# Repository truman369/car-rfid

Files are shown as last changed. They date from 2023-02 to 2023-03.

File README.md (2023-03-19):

# RFID Car Lock

This project is an Arduino-based device that controls a car lock using an RFID reader. It allows for keyless entry to the car by reading an RFID tag and unlocking the doors if the tag matches the authorized tag in the system.

## Hardware Requirements

To build this project, I used the following components:

- Arduino Nano
- Ironlogic CP-Z-2 RFID 125 Khz reader
- Standard 5-wire car lock actuator
- TZT 5V 4 channel relay module
- Mini360 DC-DC step down converter
- Standard passive buzzer
- Breadboard, wires, male and female pins, jumper, button, screw connectors

## Circuit Diagram

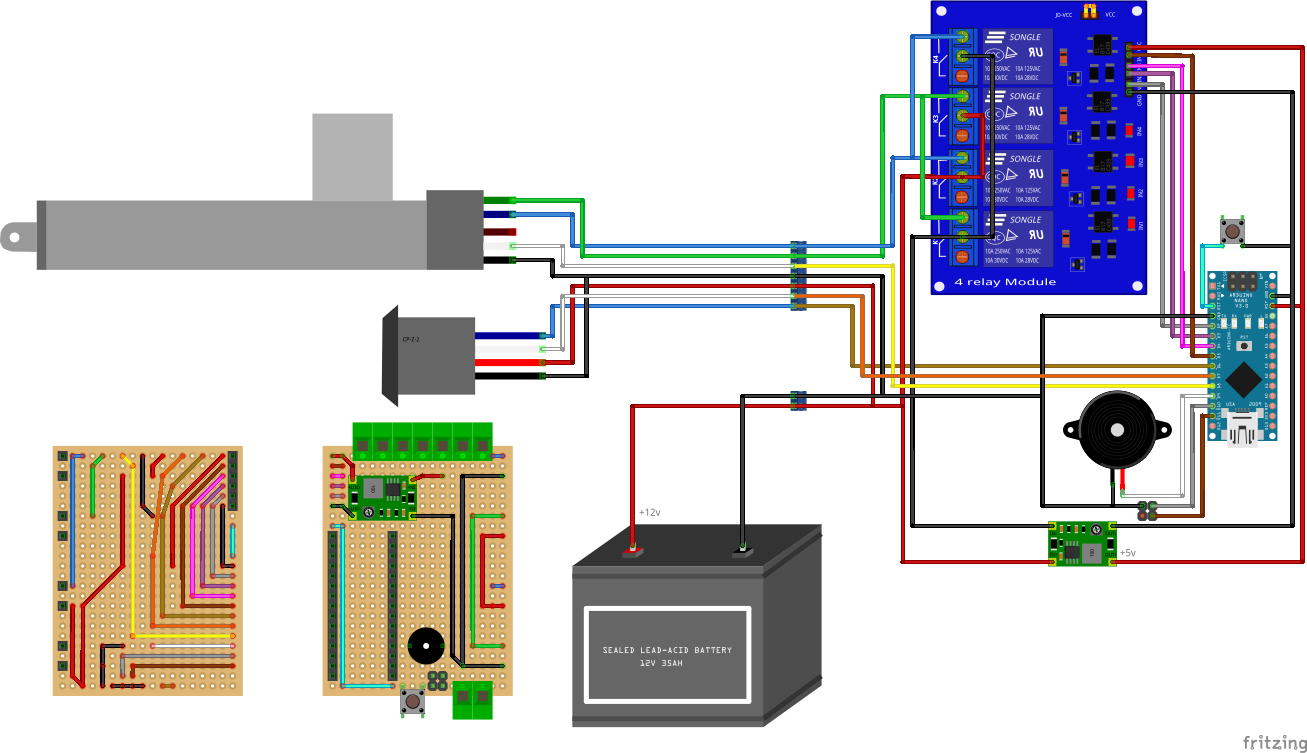
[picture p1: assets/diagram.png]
Circuit Diagram


Ironlogic CP-Z-2 reader operates in DS-1990A emulation mode and sends the key code via D1 (white) using the 1-wire protocol. D0 (blue) is used to wake up the Arduino controller from deep sleep mode.

The lock is controlled through a relay module by applying direct and inverted voltage to the actuator wires (green and blue). The white wire of the actuator is used to read the current lock position (open/closed).

The jumper is used to set the operating modes. The button is used to reboot the device. The buzzer is used for device status indication.

## Software Requirements

External libraries used in the project:
- [OneWire](https://github.com/paulstoffregen/OneWire)
- [LowPower](https://github.com/LowPowerLab/LowPower)

To build and upload the project, you can use the following components:

- [PlatformIO Core](https://docs.platformio.org/en/latest/core/installation.html)
- [Visual Studio Code](https://code.visualstudio.com/) 

## Installation

1. Clone the repository to your local machine.
2. Connect the Arduino to your computer using a USB cable.
3. Make sure that the Arduino is properly recognized by your system.
4. Open the project folder in Visual Studio Code.
5. In VS Code, open the Terminal and run the command `pio run` to build the project.

## Usage

Set up operating mode using the jumper and reboot the device.

Jumper Position

### Normal mode

No jumper or pins 3-4 are shorted. On startup the buzzer emits one short beep.

When applying an rfid key, if the key is authorized, the lock changes its state and the buzzer emits long high tone beep.

If the key is not authorized, or opening/closing the lock failed, the buzzer emits long low tone beep.

### Add keys

Jumper is set to short 2-4 pins. On startup the buzzer emits two short beeps: one medium and one high tone.

When applying an rfid key, one short beep sounds and device try to save the key. After that:

- Long high tone beep - the key was successfully written to memory.

- Long low tone beep - the key already exists, or max count of keys reached.

### Remove keys

Jumper is set to short 1-3 pins. On startup the buzzer emits three short beeps: one medium and two high tone.

When applying an rfid key, two short beep sounds and device try to remove the key from memory. After that:

- Long high tone beep - the key was successfully removed from memory.

- Long low tone beep - the key not found.

### Full reset

Jumper is set to short 1-2 pins. On startup the buzzer emits five short beeps: one medium tone and four high ones. After that, the device EEPROM is completely erased.

## 3D Printed Case

I made a very simple case for 3D printing, but it needs some modification in place. Here are STL files:

- [Lower Body](assets/car_rfid_case_1.stl)
- [Top Case](assets/car_rfid_case_2.stl)

## Additional images

- [Breadboard top](assets/breadboard_01.jpg)
- [Breadboard bottom](assets/breadboard_02.jpg)
- [Breadboard assembled](assets/breadboard_03.jpg)
- [3D-printed case](assets/case_01.jpg)
- [Case modification](assets/case_02.jpg)

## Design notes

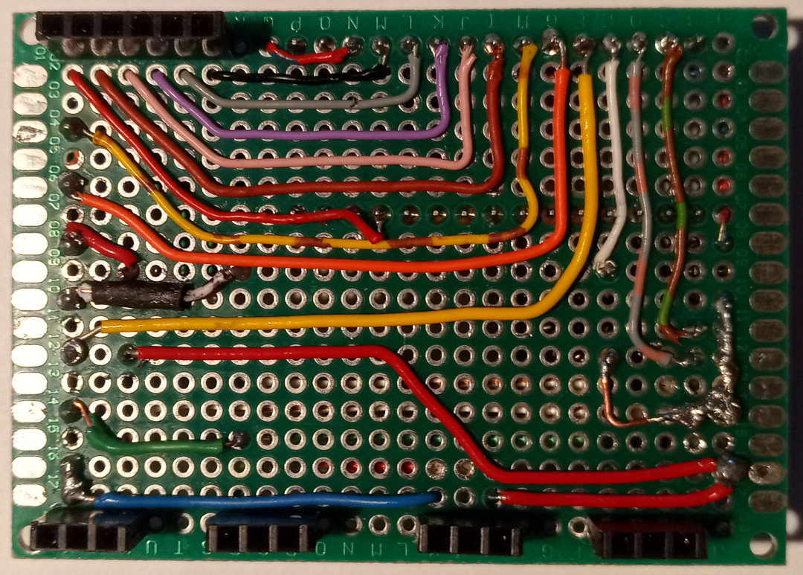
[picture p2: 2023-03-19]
assets/breadboard_02.jpg

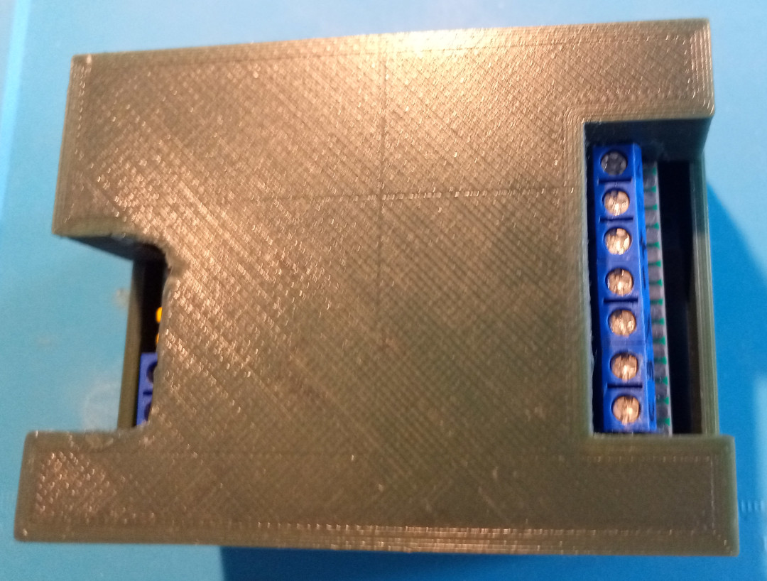
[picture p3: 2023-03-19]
assets/case_01.jpg

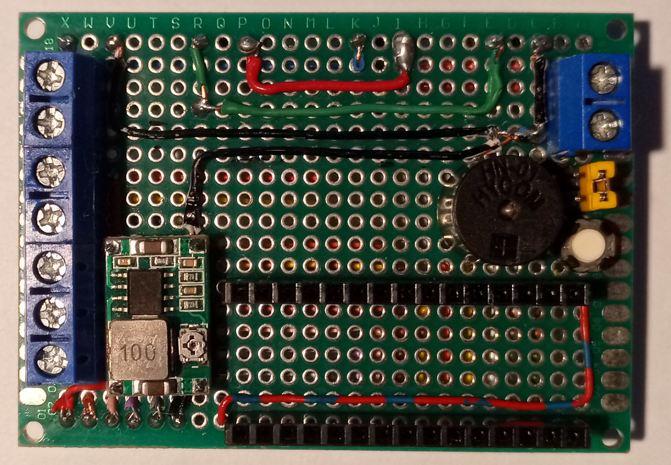
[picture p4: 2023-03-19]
assets/breadboard_01.jpg

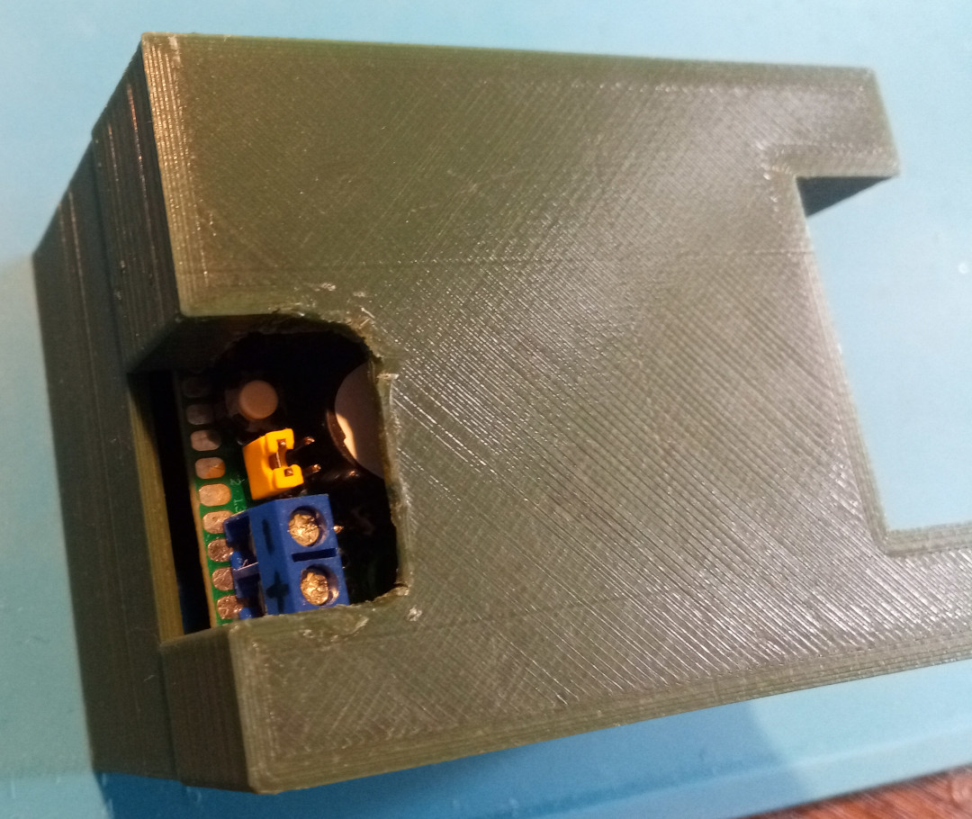
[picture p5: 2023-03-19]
assets/case_02.jpg

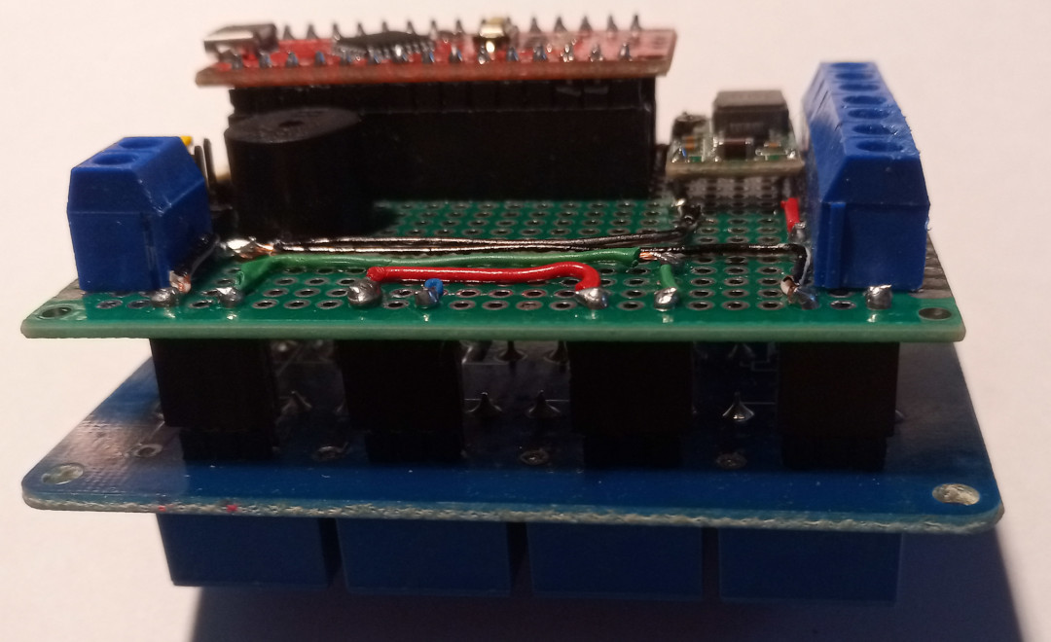
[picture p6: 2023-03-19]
assets/breadboard_03.jpg

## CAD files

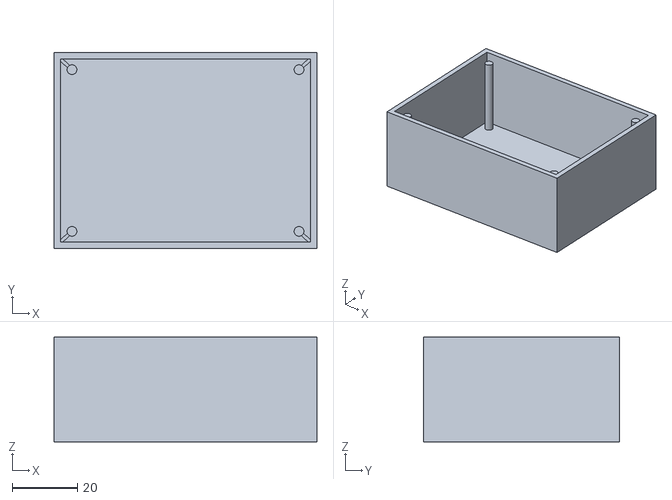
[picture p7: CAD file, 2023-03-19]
assets/car_rfid_case_1.stl
80.5 x 60.0 x 32.0

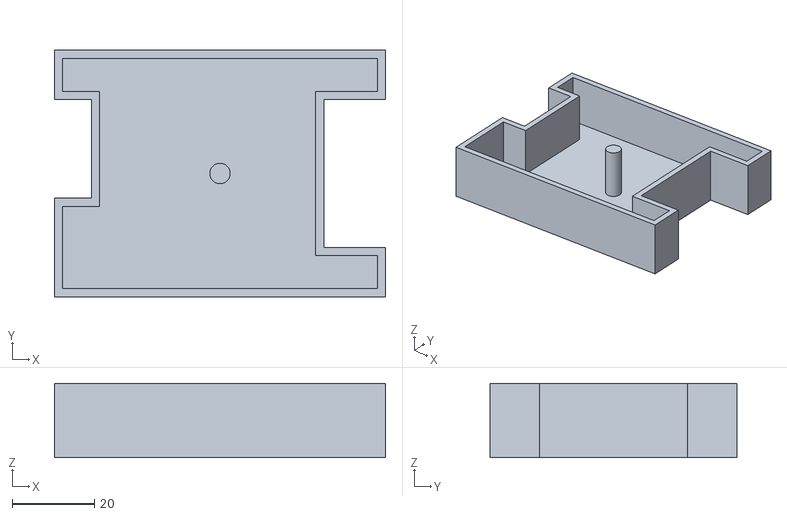
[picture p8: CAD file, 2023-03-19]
assets/car_rfid_case_2.stl
80.5 x 60.0 x 18.0

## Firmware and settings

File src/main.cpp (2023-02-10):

#include <Arduino.h>
#include <OneWire.h>
#include <LowPower.h>
#include <EEPROM.h>

#define READER_DELAY 1000 // delay while reader is sending the same key code
#define LOCK_DELAY 500    // impulse duration for lock moving
#define HIGH_TONE 2000    // high frequency for buzzer
#define LOW_TONE 200      // low frequency for buzzer

#define KEY_CNT_ADDR 511 // EEPROM address for saved keys count
#define KEY_MAX_CNT 10   // max count of keys to save
#define KEY_LENGTH 8     // key length in bytes
#define KEY_S_ADDR 0     // EEPROM start address for saved keys

#define WAKEUP_PIN 6       // wake up pin for external interrupt (D0 from reader)
#define VECTOR PCINT2_vect // alias for PCINT vector PCINT2 (D02-D07) <= WAKEUP_PIN
#define PCMSK PCMSK2       // alias for PCMSK (PCINT2)
#define DALLAS_PIN 7       // dallas ibutton 1-wire pin (D1 from reader)
#define LOCK_STATUS_PIN 8  // normal opened pin, connected to GND when lock is closed
#define BUZZER_PIN 9       // buzzer pin
#define JP1_PIN 10         // cfg pin
#define JP2_PIN 11         // cfg pin

// |   0   |   1   |   2   |   3   |   4   |
// |       |    _  |  _    |  _ _  |       |
// |  . .  |  . .  |  . .  |  . .  | |. .| |
// | |. .| |  . .  |  . .  |  . .  |  . .  |
// |       |    —  |  —    |  — —  |       |

#define MODE_NORMAL 0 // normal mode (no jumper or bottom)
#define MODE_ADD 1    // adding new keys (right jumper)
#define MODE_REMOVE 2 // removing keys (left jumper)
#define MODE_UNUSED 3 // reserved for future (left+right jumpers)
#define MODE_WIPE 4   // clear EEPROM (top jumper)

// relay module pins to move lock, need to send LOW signal
// first pair to open, second pair to close
const byte RELAY_PINS[4] = {2, 3, 4, 5};

// aliases
#define OPEN_LOCK moveLock(RELAY_PINS[0], RELAY_PINS[1])
#define CLOSE_LOCK moveLock(RELAY_PINS[2], RELAY_PINS[3])
#define LOCK_IS_OPENED digitalRead(LOCK_STATUS_PIN)

OneWire ds(DALLAS_PIN); // dallas ibutton wire
byte mode = 0;          // device operating mode
byte key_count = 0;     // count of saved keys
byte valid_keys[KEY_MAX_CNT][KEY_LENGTH];

// print hex key to //Serial
// void printKey(byte *key)
// {
//   for (byte i = 0; i < KEY_LENGTH; i++)
//   {
//     if (key[i] < 0x10)
//     {
//       Serial.print('0'); // print leading zero
//     }
//     Serial.print(key[i], HEX); // print byte
//     Serial.print(' ');         // space between bytes
//   }
//   // Serial.println();
// }

// move lock via relay pins
void moveLock(byte pin1, byte pin2)
{
  digitalWrite(pin1, LOW); // power up solenoid
  digitalWrite(pin2, LOW);
  delay(LOCK_DELAY);        // wait for lock moving
  digitalWrite(pin1, HIGH); // power down solenoid
  digitalWrite(pin2, HIGH);
}

// external interrupt handler for PCIINT2 (D02-D07)
ISR(VECTOR) {}

// wipe EEPROM
void wipeEEPROM()
{
  EEPROM.update(KEY_CNT_ADDR, 0);
  byte data[KEY_MAX_CNT * KEY_LENGTH];
  memset(data, 0, sizeof(data));
  EEPROM.put(KEY_S_ADDR, data);
  // Serial.println("EEPROM data cleared");
}

// beep for mode recognition
void modeBeep(byte mode)
{
  for (byte i = 0; i < mode; i++)
  {
    tone(BUZZER_PIN, 1000);
    delay(50);
    noTone(BUZZER_PIN);
    delay(50);
  }
}

// check for valid key
bool keyIsValid(byte *key)
{
  bool isValid = false;
  for (byte i = 0; i < sizeof(valid_keys) / KEY_LENGTH; i++)
  {
    if (memcmp(key, valid_keys[i], KEY_LENGTH) == 0)
    {
      isValid = true;
      break; // don't check other keys
    }
  }
  return isValid;
}

// add key handler
bool addKey(byte *key)
{
  if (keyIsValid(key))
  {
    // Serial.println("Key already exists!");
    return false;
  }
  else if (key_count == KEY_MAX_CNT)
  {
    // Serial.println("Max count of keys reached!");
    return false;
  }
  for (byte i = 0; i < KEY_LENGTH; i++)
  {
    valid_keys[key_count][i] = key[i];
  }
  EEPROM.put(KEY_S_ADDR, valid_keys);
  key_count++;
  EEPROM.put(KEY_CNT_ADDR, key_count);
  // Serial.println("Key added");
  return true;
}

// remove key handler
bool removeKey(byte *key)
{
  bool flag = false;
  for (byte i = 0; i < sizeof(valid_keys) / KEY_LENGTH; i++)
  {
    if (flag || memcmp(key, valid_keys[i], KEY_LENGTH) == 0)
    {
      flag = true;
      for (byte j = 0; j < KEY_LENGTH; j++)
      {
        valid_keys[i][j] = valid_keys[i + 1][j];
      }
    }
  }
  if (flag)
  {
    for (byte i = 0; i < KEY_LENGTH; i++)
    {
      valid_keys[key_count][i] = 0;
    }
    EEPROM.put(KEY_S_ADDR, valid_keys);
    key_count--;
    EEPROM.put(KEY_CNT_ADDR, key_count);
    // Serial.println("Key removed");
    return true;
  }
  // Serial.println("Key not found");
  return false;
}

// normal mode handler
bool lockHandler(byte *key)
{
  if (keyIsValid(key))
  {
    if (LOCK_IS_OPENED)
    {
      // Serial.println("Lock is opened, closing...");
      CLOSE_LOCK;
      if (!LOCK_IS_OPENED)
      {
        // Serial.println("Lock closed sucessfully");
        return true;
      }
      else
      {
        // Serial.println("Failed to close lock");
        return false;
      }
    }
    else
    {
      // Serial.println("Lock is closed, opening...");
      OPEN_LOCK;
      if (LOCK_IS_OPENED)
      {
        // Serial.println("Lock opened sucessfully");
        return true;
      }
      else
      {
        // Serial.println("Failed to open lock");
        return false;
      }
    }
  }
  else
  {
    // Serial.println("Invalid key");
    return false;
  }
}

void setup()
{
  // Serial.begin(9600);
  // Serial.println("Loading...");
  for (byte pin : RELAY_PINS)
  {
    pinMode(pin, OUTPUT);    // init relay pins
    digitalWrite(pin, HIGH); // HIGH - relay is disabled
  }
  pinMode(LOCK_STATUS_PIN, INPUT_PULLUP);

  // check configuration jumper
  pinMode(JP1_PIN, INPUT_PULLUP);
  pinMode(JP2_PIN, INPUT_PULLUP);
  mode += !digitalRead(JP1_PIN);
  mode += !digitalRead(JP2_PIN) * 2;
  if (mode == 0)
  { // check if cfg pins are connected to each other
    pinMode(JP1_PIN, OUTPUT);
    digitalWrite(JP1_PIN, LOW);
    mode += !digitalRead(JP2_PIN) * 4;
  }
  // Serial.println("Mode: " + String(mode));

  // clear EEPROM on wipe mode
  if (mode == MODE_WIPE)
  {
    wipeEEPROM();
  }

  // get key count from EEPROM
  key_count = EEPROM.read(KEY_CNT_ADDR);
  if (key_count > KEY_MAX_CNT)
  { // flush keys on incorrect value
    key_count = 0;
    wipeEEPROM();
  }

  // read saved keys from EEPROM
  EEPROM.get(KEY_S_ADDR, valid_keys);

  // Serial.println("Saved keys:");
  //  for (byte i = 0; i < key_count; i++)
  //  {
  //    printKey(valid_keys[i]);
  //  }

  pinMode(WAKEUP_PIN, INPUT_PULLUP);                // init wake up pin for interrupts
  PCICR |= (1 << digitalPinToPCICRbit(WAKEUP_PIN)); // enable PCINT interrupt for group
  PCMSK |= (1 << digitalPinToPCMSKbit(WAKEUP_PIN)); // enable PCINT interrupt for pin

  tone(BUZZER_PIN, 500); // startup beep
  delay(50);
  noTone(BUZZER_PIN);
  modeBeep(mode);
  // delay(500);
}

void loop()
{
  // sleep and wake up on external interrupt by reader
  LowPower.powerDown(SLEEP_FOREVER, ADC_OFF, BOD_OFF);
  delay(50); // delay for wake up
  // Serial.println("Wake up, Neo!");
  if (ds.reset())
  {                 // if card is detected
    ds.write(0x33); // send reader cmd to receive card data
    // read 8 bytes of dallas key
    byte key_buf[KEY_LENGTH]; // key buffer
    for (byte i = 0; i < KEY_LENGTH; i++)
    {
      key_buf[i] = ds.read();
    }
    // check family key and CRC
    if (key_buf[0] == 0x01 && key_buf[KEY_LENGTH - 1] == ds.crc8(key_buf, KEY_LENGTH - 1))
    {
      bool res; // result of handler
      switch (mode)
      {
      case MODE_NORMAL:
        res = lockHandler(key_buf);
        break;
      case MODE_ADD:
        res = addKey(key_buf);
        break;
      case MODE_REMOVE:
        res = removeKey(key_buf);
        break;
      default:
        break;
      }
      modeBeep(mode);
      // beep with high tone on ok and low tone on fail
      uint16_t toneFreq;
      toneFreq = (res) ? HIGH_TONE : LOW_TONE;
      tone(BUZZER_PIN, toneFreq);
      delay(READER_DELAY); // delay while reader is sending the same key
      noTone(BUZZER_PIN);
    }
  }
}
